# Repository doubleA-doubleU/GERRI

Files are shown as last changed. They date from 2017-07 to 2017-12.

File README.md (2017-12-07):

## GERRI (Guidance Enabled Robotic Raceline Interpreter)
#### _Aaron Weatherly_
#### _Northwestern University_

<p>
<br>

<br>
</p>

## Overview
This project allows an off-the-shelf radio controlled car to be converted
into an autonomous vehicle. This is accomplished by replacing the car's 
control system with an Android phone and a PIC32 microcontroller. External
localization is done through HTC vive position sensors. Check out this 
[video][youtube] for a demonstration.

## Required Components 
1. Android phone (I used a Samsung Galaxy S5)
2. Radio Controlled Car (I used a Tamiya TL01)
3. USB OTG cable - micro to mini
4. 3D printed [phone and PCB mounts][parts]
5. Microchip [PIC32MX250F128B][pic] microcontroller in 28-pin SPDIP package
6. VNH5019 [Motor Driver Carrier][hbridge]
7. HTC Vive [Base Station][base]
8. 2x HTC Vive Position Sensor, [TS3633-CM1][vive]
9. Custom [PCB][pcb] with mounting holes for:
	* 28 Pin DIP socket
	* Mini USB connector
	* Slideswitch
	* MCP1702 voltage regulator (TO92)
	* 3mm red LED with 330 Ohm resistor
	* Reset button with 10 kOhm resistor
	* 3mm green LED with 330 Ohm resistor
	* User button with 10 kOhm resistor
	* 8 MHz crystal resonator
	* 4x 0.1 uF capacitors
	* 2x 10 uF polarized capacitors
	* 5-pin breakout for PICkit3 programmer
	* 2x 8-pin breakouts for remaining I/O pins and power/ground connections

## Software
#### In MPLAB X IDE:
1. Create new 32-bit MPLAB Harmony project, named GERRI, for the PIC32MX250F128B
2. Generate code
3. Copy all code from the provided [app.c][appc], [app.h][apph], 
[main.c][main], [default.mhc][default], [system_config.h][config], 
and [system_interrupt.c][interrupt]	into the auto-generated Harmony 
files of same names
4. Install the project onto the PIC
	
#### In Android Studio:
1. Create new project with an Empty Activity, named GERRI
2. Copy the provided [classes.jar][classes] to <your_local_project_path>/GERRI/app/libs/
3. In the IDE, navigate the left panel to Project/GERRI/app/libs/
4. Right click classes.jar, Add as Library, Add to Module: app
5. In the IDE, navigate the left panel to Android/app/res/
6. Right click res, add driectory, name it "xml"
7. Right click xml, add new XML Resource file, name it "device_filter.xml"
8. Open this new xml file and replace the contents with the code from 
the provided [device_filter.xml][filter] file
9. Copy all code from the provided [activity_main.xml][layout], 
[AndroidManifest.xml][manifest], and [MainActivity.java][java] into 
the auto-generated Android Studio files of same name.

## Under the Hood
This is an extension of a much simpler line-following [robot][pathfinder].

#### The Android app:
GERRI begins by using the phone's camera to identify the track ahead. For
me, the track was designated by blue painter's tape, so the key 
lines from `MainActivity.java` are:
```java
for (int startY = 180; startY <= 300; startY = startY + 20) { // which row in the bitmap to analyze to read
    bmp.getPixels(pixels, 0, bmp.getWidth(), 0, startY, bmp.getWidth(), 1);
    // in the row, see if the pixel is blue
    for (int i = 0; i < bmp.getWidth(); i++) {
        if (blue(pixels[i]) > thresh) {
            pixels[i] = rgb(0, 255, 0); // over write the pixel with pure green
            // COM pixel calculation
            M = M + 1;
            sum = sum + i;
        }
    }
    // update the row
    bmp.setPixels(pixels, 0, bmp.getWidth(), 0, startY, bmp.getWidth(), 1);

    // calculate COM for each row
    if (M == 0) {
        COM = 0;
    } else {
        COM = (sum / M) + 1;
        COMavg += COM;
        count++;
    }
}
```
This loop occurs each time there is a new camera frame. We analyze several
rows of pixels, identify which ones are blue, then calculate the average
position for the portion of the track that can be seen. Then, the following
uses a fixed transform from the camera frame to the world frame to determine
where the track is and add that point to a bitmap representing the track:
```java
// average the COMs
if (count == 0) {
    COMavg = 0;
} else {
    COMavg = COMavg / count;
    // calculate a point on the track based on COMavg, xCar, yCar, theta
    float l = (float) (0.025*COMavg); // distance from left of frame to the COM (in cm)
    float d = (float) (Math.sqrt(Math.pow(18.2,2) - Math.pow(l,2))); // distance from the car to the COM (in cm)
    float theta2 = (float) (Math.atan2(8-l,16.35)); // angle from the car to the COM along a line 16.35 cm from car's position (in radians)
    xTrack = (int) (xCar*100 + d*Math.cos(theta + theta2) + 0.5);
    yTrack = (int) (yCar*100 - 200 + d*Math.sin(theta + theta2) +0.5);
    if (lapTime<0.1) {
        xInit = xTrack;
        yInit = yTrack;
    }
    // add that point to the track bitmap
    if (c2 != null) {
		try {
			bmp2.setPixel(xTrack, yTrack, 0xffffffff);
		} catch (Exception e) {}
    }
}
// draw circle at COM
canvas.drawCircle(COMavg, 240, 5, paint1);
// write the COM as text
canvas.drawText("COM = " + COMavg, 10, 30, paint1);
//send COM to PIC
String sendString = String.valueOf(COMavg) + '\n';
try {
    sPort.write(sendString.getBytes(), 1); // 1 is the timeout
} catch (IOException e) {}
```
This process continues until GERRI has completed its first lap and generated
a map of the entire track. It then switches modes from simple line-following 
to a proportional feedback controller that uses the track bitmap as the desired
path. The first step in this phase is to find the nearest point on the track
from the car's current position:
```java
// find nearest white pixel in bmp2 by looking at the rings of pixels around current location
int x = (int) (xCar*100 + 0.5); // convert to cm
int y = (int) (yCar*100 - 200 + 0.5); // convert to cm, shift to fit the bitmap's range
outerLoop:
for (int ring=0; ring<15;ring++) { // looking within 15cm radius
    int[] pixels = new int[2*ring+1];
    for (int row = -ring; row <= ring; row++) {
        try {
            bmp2.getPixels(pixels,0,bmp2.getWidth(),x-ring,y+row,2*ring+1,1);
        } catch (IllegalArgumentException iae) {} // sometimes the data is bad...
        for (int col = -ring; col <= ring; col++) {
            if (pixels[col+ring] == 0xffffffff) {
                // if the pixel is white, define (xDesired,yDesired) as the current row and column of the search
                xDesired = x+col;
                yDesired = y+row;
                if (xDesired_prev == 0) {
                    xDesired_prev = xDesired;
                    yDesired_prev = yDesired;
                }
                // break the both for loops once the track is found
                break outerLoop;
            }
        }
    }
}
```
Next, we calculate the position and angular error as follows:
```java
// calculate position error
posError = (float) Math.sqrt(Math.pow(xDesired - x,2) + Math.pow(yDesired - y,2));

if (posError != 0 && xDesired - xDesired_prev != 0) {
	// calculate desired angle based on current vs previous track points
    thetaDesired = (float) Math.atan2(yDesired - yDesired_prev, xDesired - xDesired_prev);
    if (Math.abs(thetaDesired-thetaDesired_prev) > 0.5) {
        thetaDesired = thetaDesired_prev;
    }
    // calculate angular error
    angError = thetaDesired - theta;
} else {
    if (thetaDesired_prev == 0){
        thetaDesired = theta;
        angError = 0;
    }
    else {
        thetaDesired = thetaDesired_prev;
        angError = thetaDesired - theta;
    }
}
```
Now we have to determine whether the position error should be positive or
negative by determining whether the track is to the left or right of the
car. There is a hard coded assumption here that the track direction is 
always counterclockwise. This was to simplify the if statements below:
```java
// determine whether track is to the left or right (assuming counterclockwise track direction...)
float theta2 = (float) Math.atan2(yDesired - y, xDesired - x); // angle from car to the track
if (thetaDesired >= Math.PI/2 && thetaDesired < Math.PI) {
    if (theta2 >= Math.PI && theta2 < 3*Math.PI/2) { // the track is to the left of the car
        posError = (-1)*posError;
    }
}
else if (thetaDesired >= Math.PI && thetaDesired < 3*Math.PI/2) {
	if (theta2 >= -Math.PI/2 && theta2 < 0) { // the track is to the left of the car
        posError = (-1)*posError;
    }
}
else if (thetaDesired >= -Math.PI/2 && thetaDesired < 0) {
    if (theta2 >=0 && theta2 < Math.PI/2) { // the track is to the left of the car
        posError = (-1)*posError;
    }
}
else if (thetaDesired >= 0 && thetaDesired < Math.PI/2) {
    if (theta2 >= Math.PI/2 && theta2 < Math.PI) { // the track is to the left of the car
        posError = (-1)*posError;
	}
}
```
Finally, we apply the proportional controller based on the [Stanley method][stanley]
from Stanford's entry into the DARPA Grand Challenge.
```java
// use proportional control to calculate a steering angle value between 0 and 640 based on angError (rad) and posError (cm)
// using the Stanley method: http://robots.stanford.edu/papers/thrun.stanley05.pdf
float cmdRad = angError + (float) Math.atan(thresh2*posError/500); // assuming constant velocity, thresh2 is the proportional gain
float cmdDeg = cmdRad*180/((float) Math.PI);
int cmd;
if (cmdDeg <= -30) {
    cmd = 640;
} else if (cmdDeg >= 30) {
	cmd = 1;
} else {
    cmd = (int) (-320*cmdDeg/30 + 320.5);
}
// send steering command to PIC
String sendString = String.valueOf(cmd) + '\n';
try {
    sPort.write(sendString.getBytes(), 1); // 1 is the timeout
} catch (IOException e) {}
```
In both the mapping and controlled cases, the output of the Android app 
is an integer between 0 and 640 that is proportional to desired steering 
angles between positive and negative 30 degrees that is sent to the PIC.

#### The PIC32 firmware:
The PIC32 communicates with the Android app via USB. It takes the integer value
provided by the app and controlls the motor speed/direction and the servo steering 
angle as shown below (from `app.c`):
```c
if (gotRx) { // rxVal should be an int between 0 and 640 (setting motor speed and steering angle from Center of Mass)
    if (rxVal > 640) {          // stop button pressed, no movement, center the steering, reset lap time
        duty = 0;
        LATAbits.LATA1 = 0;
        LATBbits.LATB2 = 1;
        OC3RS = 1000;
        go = 0;
        lapTime = 0.0;
    } else if (rxVal <= 0) {    // reverse direction and previous steering command to find the line again
        duty = 20;
        LATAbits.LATA1 = 1;     // reverse drive motion
        LATBbits.LATB2 = 0;     // reverse drive motion
        rxVal = rxValPrev;
        OC3RS = 680 + rxValPrev;
        go = 1;
    } else {                    // steer towards the COM
        duty = 20;
        LATAbits.LATA1 = 0;     // forward drive motion
        LATBbits.LATB2 = 1;     // forward drive motion
        OC3RS = 1320 - rxVal;   // ranges from 680 to 1320
        go = 1;
    }
	OC1RS = duty*40;            // convert duty cycle based on period register

    rxPos = 0;
    gotRx = 0; // clear the flag
    rxValPrev = rxVal;
    for (j = 0; j < 64; j++) {
        rx[j] = 0; // clear the array
    }
}
```
The PIC32 also provides the position (x,y,theta) as well as the current lap time to the
Android app via USB (also from `app.c`):
```c
// calculate position
x_pos[0] = (LIGHTHOUSEHEIGHT*sin((x_ang[0])*DEG_TO_RAD))/(sin((60+LIGHTHOUSEANGLE-x_ang[0])*DEG_TO_RAD)*sin((120-LIGHTHOUSEANGLE)*DEG_TO_RAD));
y_pos[0] = (2*LIGHTHOUSEHEIGHT*sin(y_ang[0]*DEG_TO_RAD))/sin((150-y_ang[0])*DEG_TO_RAD);
x_pos[1] = (LIGHTHOUSEHEIGHT*sin((x_ang[1])*DEG_TO_RAD))/(sin((60+LIGHTHOUSEANGLE-x_ang[1])*DEG_TO_RAD)*sin((120-LIGHTHOUSEANGLE)*DEG_TO_RAD));
y_pos[1] = (2*LIGHTHOUSEHEIGHT*sin(y_ang[1]*DEG_TO_RAD))/sin((150-y_ang[1])*DEG_TO_RAD);
x = (x_pos[0] + x_pos[1])/2.0;
y = (y_pos[0] + y_pos[1])/2.0;
        
// calculate angle 
if (x_pos[0] == x_pos[1] && y_pos[0] != y_pos[1]) {
	if (y_pos[0] > y_pos[1]) {
        theta = PHI;
    } else {
        theta = PHI + M_PI;
    }
} else if (y_pos[0] == y_pos[1] && x_pos[0] != x_pos[1]) {
    if (x_pos[1] > x_pos[0]){
        theta = PHI + M_PI_2;
    } else {
        theta = PHI + M_PI_2 + M_PI;
    }
} else if (x_pos[0] == x_pos[1] && y_pos[0] == y_pos[1]) {
    theta = 0.0; // should not happen, as sensors are in two different locations, unless sensors are not receiving data
} else {
    theta = atan2(y_pos[1]-y_pos[0],x_pos[1]-x_pos[0]) + PHI + M_PI_2; // always treating left sensor as origin for angle calc
}
            
// calculate lap time
lapTime = lapTime + ((float) (_CP0_GET_COUNT() - startTime)) / 24000000.0;
               
// send data to phone
len = sprintf(dataOut, "%.3f %.3f %.3f %.3f\r\n", x, y, theta, lapTime);
USB_DEVICE_CDC_Write(USB_DEVICE_CDC_INDEX_0,
    &appData.writeTransferHandle, dataOut, len,
    USB_DEVICE_CDC_TRANSFER_FLAGS_DATA_COMPLETE); 
```
The determination of position is done by `system_interrupt.c` through two ISRs,
one for each of the vive sensors. One of the ISRs is below (and the other is very
similar):
```c
void __ISR(_INPUT_CAPTURE_1_VECTOR, IPL5SOFT) IC1ISR(void) {
    static unsigned int ptsL=0;     // previous time stamp for left sensor
    static int stateL = -1;         // state of left sensor
    unsigned int tsL;               // time stamp for left sensor
    int unusedL = IC1BUF;           // the value of timer2 right now, doesn't matter
    unusedL = IC1BUF;               // read multiple times to ensure the buffer is cleared
    unusedL = IC1BUF;               // ...
    unusedL = IC1BUF;               // ...
    LATBbits.LATB13=PORTAbits.RA4;   // match the sensor signal on a debugging pin
    if (PORTAbits.RA4) {            // ignore rising edges
        IFS0bits.IC1IF = 0;         // clear interrupt flag
        return;                     // exit the ISR
    }    
    tsL = _CP0_GET_COUNT();         // get the current time
    if (ptsL > 0) {                 // won't calculate anything the first time through
        unsigned int l = tsL - ptsL;// calculate elapsed time
        if  (l > CYCLE) {           // indicates a synchronization cycle
            stateL = 0;             // prepare to read y angle (from right to left)
        } else {
            if (stateL >= 0) {
                switch (stateL) {   
                    case 0: {
                        y_ang[0]=l*0.0006;  // read y angle in degrees (0 to 120)
                        break;
                    }
                    case 2: {
                        x_ang[0]=l*0.0006;  // read x angle in degrees (0 to 120)
                        break;
                    }
                }
                stateL++;                       // cycle through states
                if (stateL >=4 ) stateL = -1;   // reset state
            }
        }
    }
    ptsL=tsL;           // set the previous time stamp for the next time through
    IFS0bits.IC1IF = 0; // clear the interrupt flag
}
```
This works because the base station conducts two infrared sweeps, one horizontal and one
vertical. By timing the pulses seen by the sensors, we can determine the angle at which the
base station "sees" the sensor in both directions. With some basic trigonometry, this can
be converted into meters. By doing this with two sensors, the car's heading can also be
determined, as seen above. 

## Future Work
Although this method allows for some autonomous features, it would be ideal to utilize the
track map that is generated to do some more detailed path planning. This could allow for 
the calculation of a racing line that is optimized to decrease the radius of curvature of 
the path and hence the required steering effort of the car.

I also considered including an accelerometer in order to detect loss of traction and 
adjust motor speed accordingly. Due to the limitations on track size based on my workspace,
I decided to use a fixed (and relatively slow) velocity. If the track size were larger,
it would be possible to modulate velocity based on the current error and speed up or slow
down based on the curvature of the track. In that scenario, an accelerometer would be quite 
useful.

[youtube]: https://youtu.be/dq8rHDOIuIY
[parts]: https://github.com/weatherman03/GERRI/tree/master/Parts
[pic]: http://www.microchipdirect.com/product/PIC32MX250F128B
[hbridge]: https://www.pololu.com/product/1451
[base]: https://www.vive.com/us/accessory/base-station/
[vive]: https://www.triadsemi.com/product/ts3633-cm1/
[pcb]: https://github.com/weatherman03/GERRI/tree/master/Eagle
[appc]: https://github.com/weatherman03/GERRI/blob/master/Harmony/app.c
[apph]: https://github.com/weatherman03/GERRI/blob/master/Harmony/app.h
[main]: https://github.com/weatherman03/GERRI/blob/master/Harmony/main.c
[default]: https://github.com/weatherman03/GERRI/blob/master/Harmony/default.mhc
[config]: https://github.com/weatherman03/GERRI/blob/master/Harmony/system_config.h
[interrupt]: https://github.com/weatherman03/GERRI/blob/master/Harmony/system_interrupt.c
[classes]: https://github.com/weatherman03/GERRI/blob/master/Android/classes.jar
[filter]: https://github.com/weatherman03/GERRI/blob/master/Android/device_filter.xml
[layout]: https://github.com/weatherman03/GERRI/blob/master/Android/activity_main.xml
[manifest]: https://github.com/weatherman03/GERRI/blob/master/Android/AndroidManifest.xml
[java]: https://github.com/weatherman03/GERRI/blob/master/Android/MainActivity.java
[pathfinder]: https://github.com/weatherman03/PathFinder
[stanley]: http://robots.stanford.edu/papers/thrun.stanley05.pdf

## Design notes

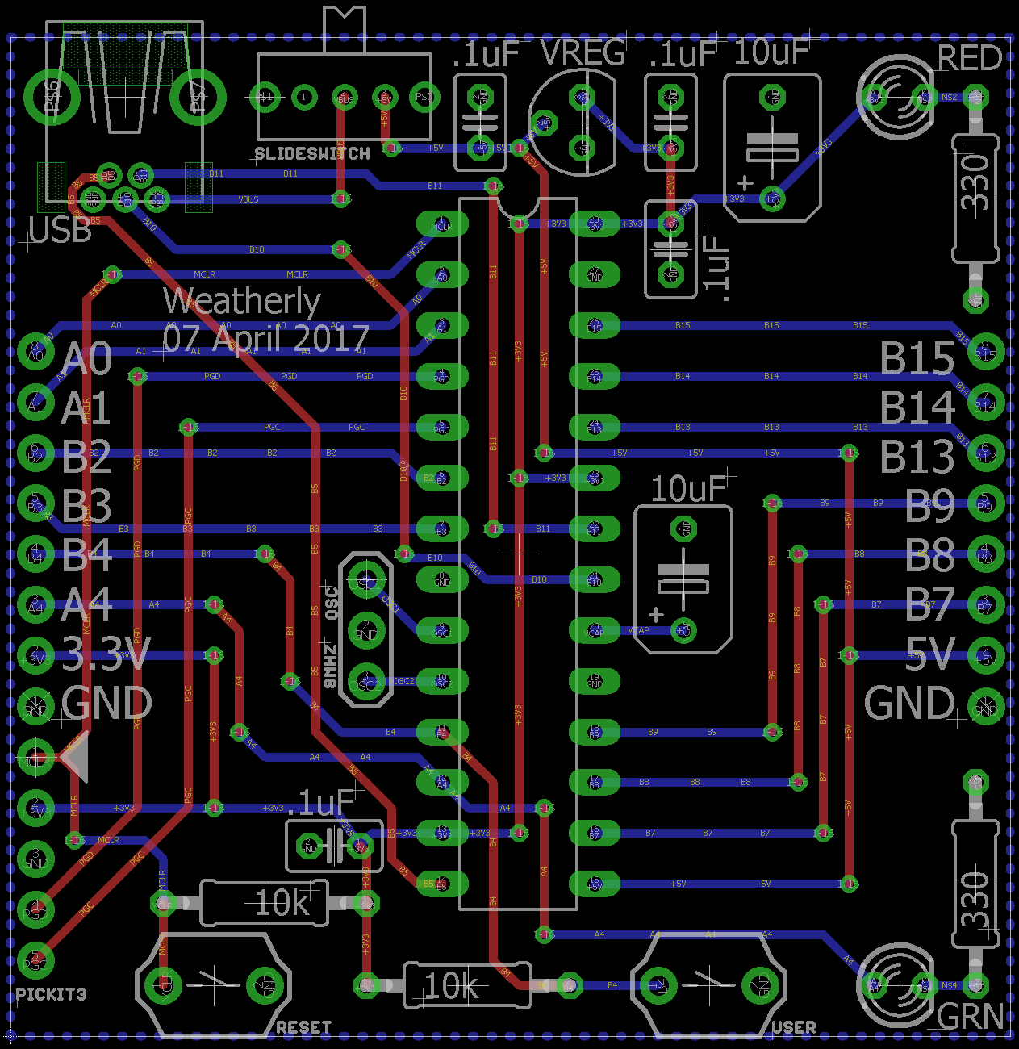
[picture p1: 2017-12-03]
Eagle/PIC32MX250F128B.png

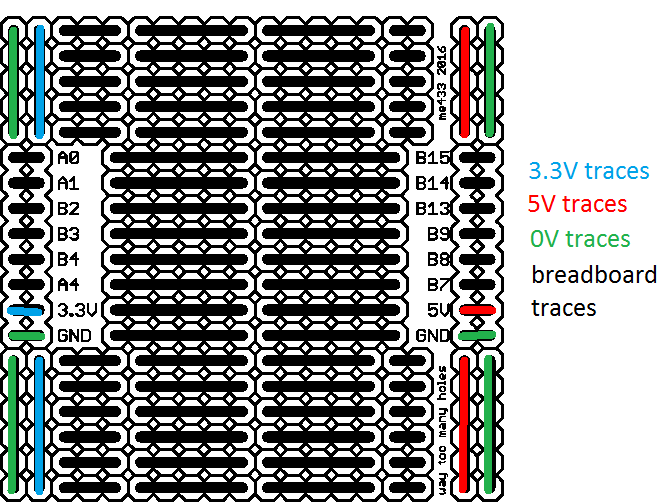
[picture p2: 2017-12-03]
Eagle/pcb_shield.png

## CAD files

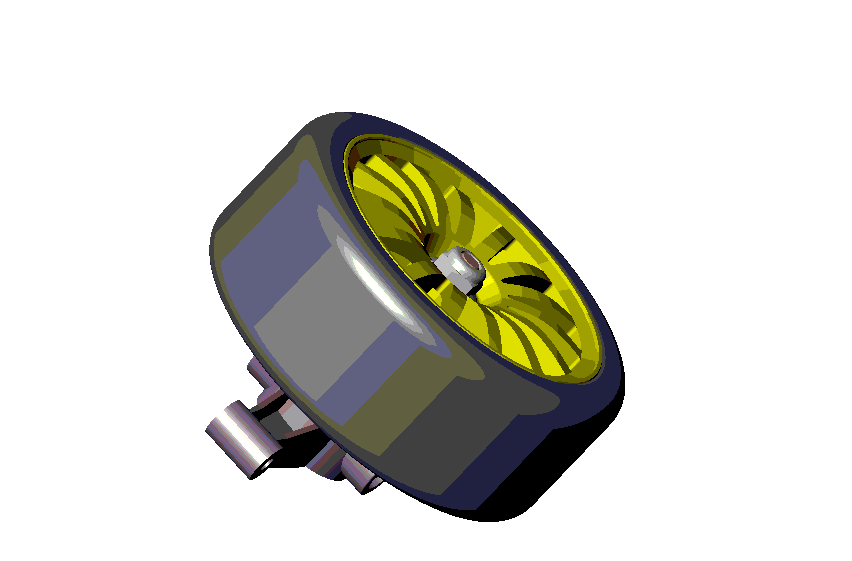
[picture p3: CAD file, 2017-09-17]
Parts/Tamiya TL01/Train-avant.SLDASM
Fusée-av-B9
Coussinet x 2
Axe de roue-MB12
Axe-2-10
Accouplement-B14
Jante
Pneu
Ecrou-MB5

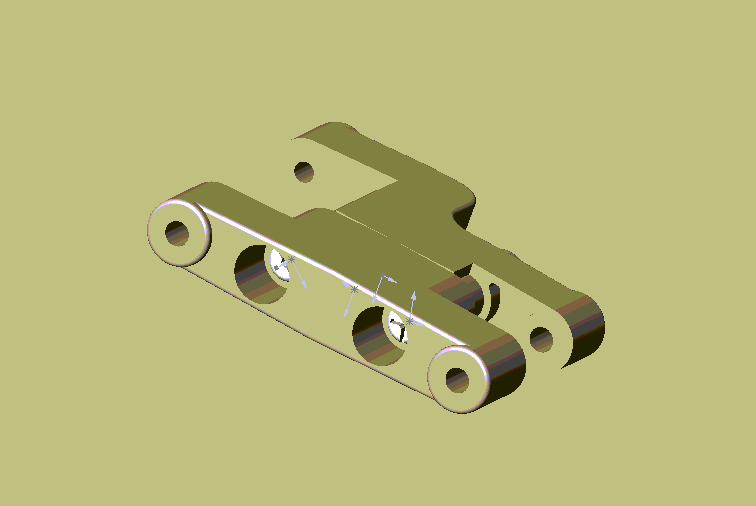
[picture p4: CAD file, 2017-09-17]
Parts/Tamiya TL01/Triangle arrière.SLDASM
Triangle arrière-C15
Triangle arrière-C14
Vis-M3-10 x 2

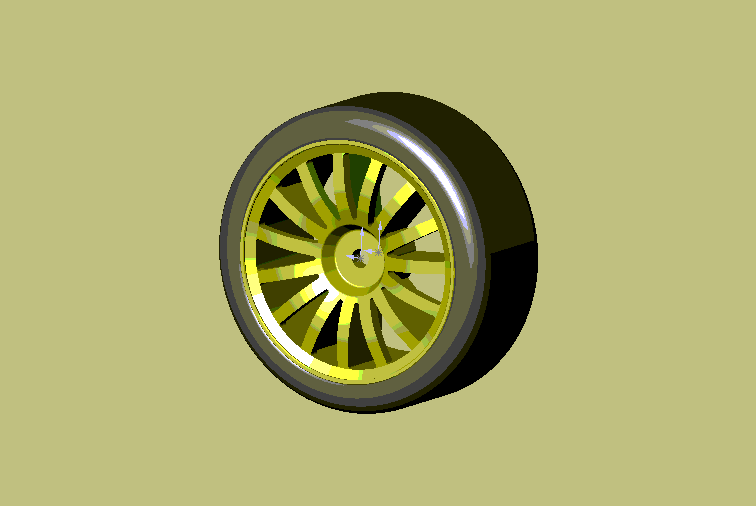
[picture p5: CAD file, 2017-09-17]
Parts/Tamiya TL01/Roue.SLDASM
Jante
Pneu

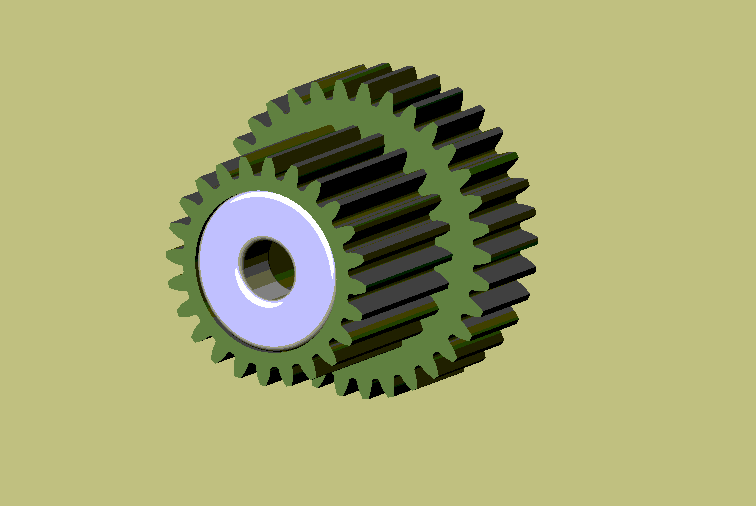
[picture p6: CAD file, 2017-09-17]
Parts/Tamiya TL01/Roue-dentée-2.SLDASM
ENG-D-24-6
ENG-D-34-6
Coussinet x 2

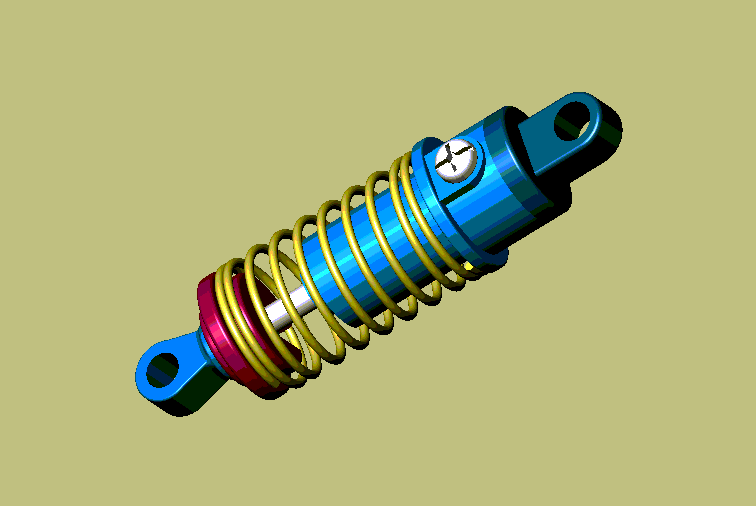
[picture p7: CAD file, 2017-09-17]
Parts/Tamiya TL01/Amortisseur.SLDASM
Corps d'amortisseur-C2
Amortisseur-MB2
Corps d'amortisseur-C1
Amortisseur-C12
Amortisseur-C9
Ressort d'amortisseur-MB14
Vis-M3-10

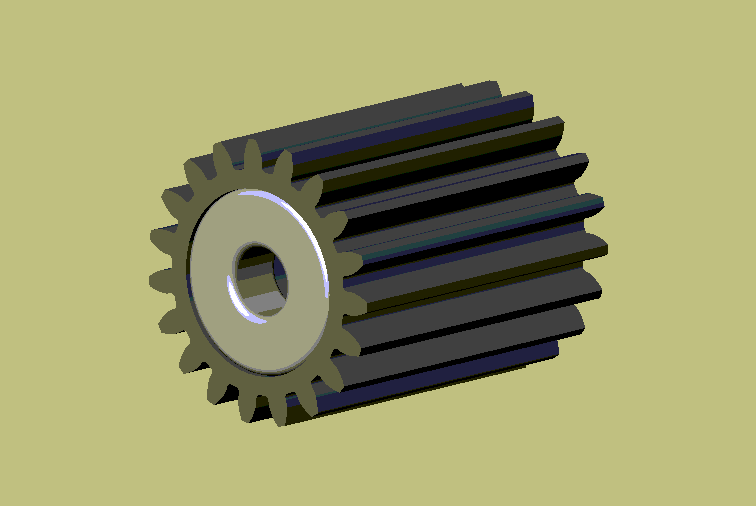
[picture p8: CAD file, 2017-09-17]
Parts/Tamiya TL01/Roue-dentée-6.SLDASM
ENG-D-19-8b
Coussinet x 2

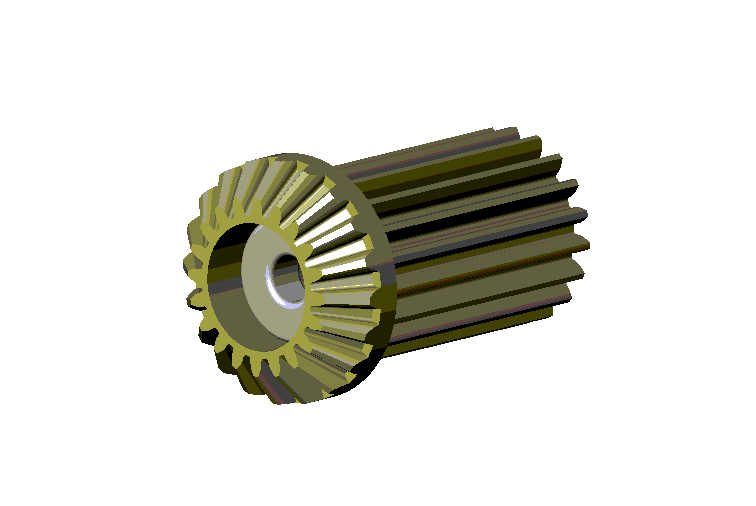
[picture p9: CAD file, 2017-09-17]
Parts/Tamiya TL01/Roue-dentée-5.SLDASM
ENG-D-19-8
ENG-C-20-45
Coussinet x 2

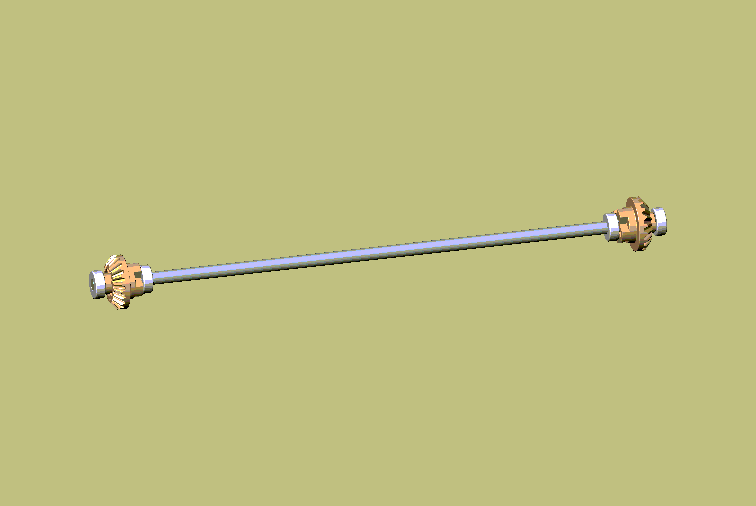
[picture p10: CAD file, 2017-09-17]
Parts/Tamiya TL01/Arbre-transmission.SLDASM
Arbre de transmission
Roue-dentée-4 x 2
Axe-2-10 x 2
Coussinet x 4

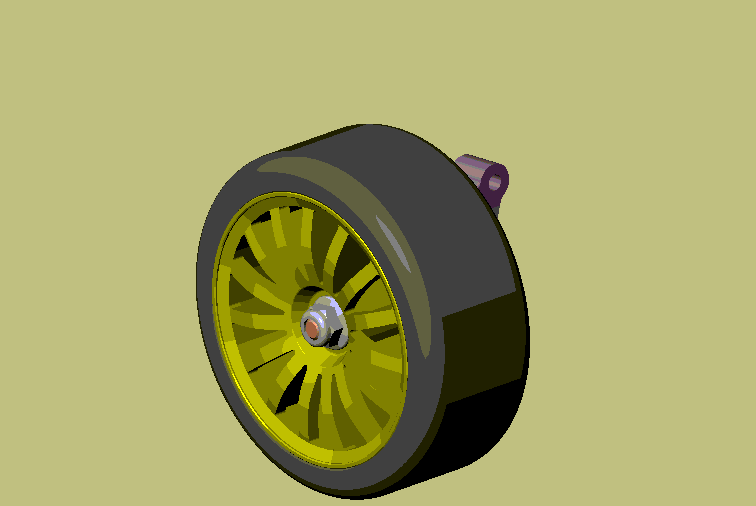
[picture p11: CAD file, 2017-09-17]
Parts/Tamiya TL01/Train-arrière.SLDASM
Fusée-ar-B4
Coussinet x 2
Axe de roue-MB12
Jante
Pneu
Ecrou-MB5
Axe-2-10
Accouplement-B14

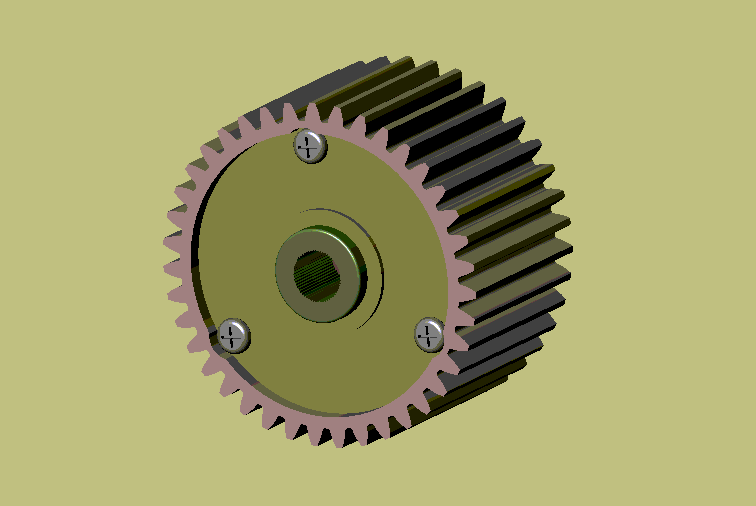
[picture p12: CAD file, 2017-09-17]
Parts/Tamiya TL01/Differentiel.SLDASM
Couronne de différentiel
Différentiel-G3
Différentiel-MA16 x 2
Différentiel-MA18
Différentiel-MA17 x 3
Vis-M2-8 x 3

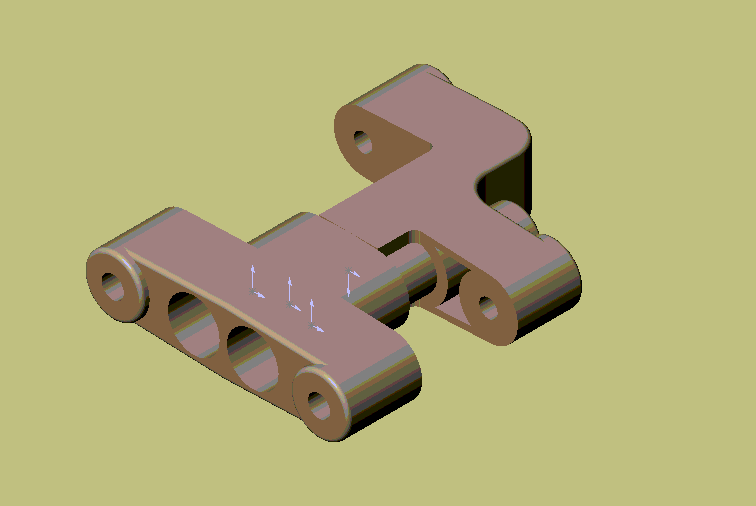
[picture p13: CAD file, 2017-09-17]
Parts/Tamiya TL01/Triangle avant.SLDASM
Triangle avant-C16
Triangle avant-C17
Vis-M3-10 x 2

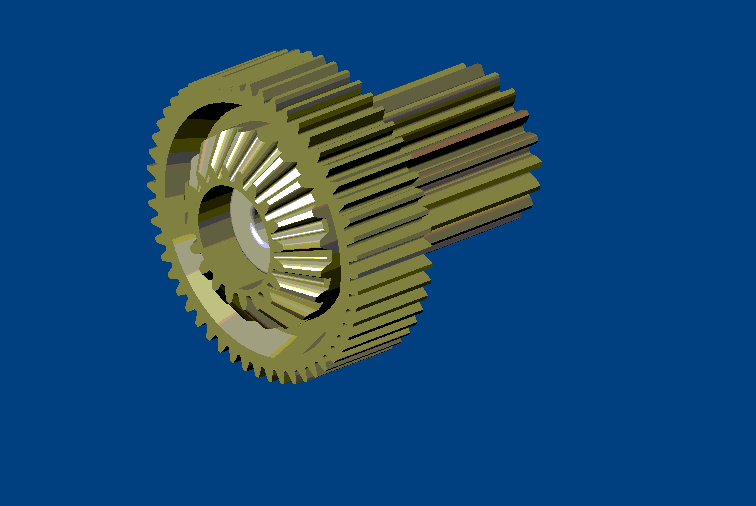
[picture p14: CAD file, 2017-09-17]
Parts/Tamiya TL01/Roue-dentée-3.SLDASM
ENG-D-52-6
ENG-D-19-8
ENG-C-20-45
Coussinet x 2

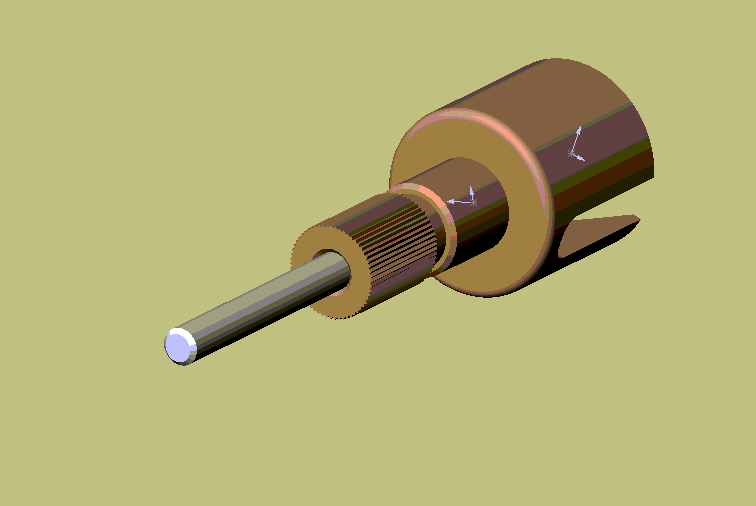
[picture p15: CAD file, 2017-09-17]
Parts/Tamiya TL01/Accouplement-MB11.SLDASM
Accouplement-MB10
Axe-2-27

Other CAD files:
Parts/Tamiya TL01/Transmission-ar-av.SLDASM
Parts/Tamiya TL01/Direction-essai.SLDASM
Parts/Tamiya TL01/Roue-dentée-3b.SLDASM
Parts/Tamiya TL01/Roue-dentée-2b.SLDASM
Parts/Tamiya TL01/Commande de direction.SLDASM
Parts/Tamiya TL01/Accouplement-B14.SLDPRT
Parts/Tamiya TL01/Accouplement-MB10.SLDPRT
Parts/Tamiya TL01/Amortisseur-C12.SLDPRT
Parts/Tamiya TL01/Amortisseur-C9.SLDPRT
Parts/Tamiya TL01/Amortisseur-MB2.SLDPRT
Parts/Tamiya TL01/Antenne-B7.SLDPRT
Parts/Tamiya TL01/Arbre d'entraînement.SLDPRT
Parts/Tamiya TL01/Arbre de transmission.SLDPRT
Parts/Tamiya TL01/Axe de roue-MB12.SLDPRT
Parts/Tamiya TL01/Axe-2-10.SLDPRT
Parts/Tamiya TL01/Axe-2-27.SLDPRT
Parts/Tamiya TL01/Axe-5-25.SLDPRT
Parts/Tamiya TL01/Axe-5-30.SLDPRT
Parts/Tamiya TL01/Axe-5-40.SLDPRT
Parts/Tamiya TL01/Bague de Servomoteur.SLDPRT
Parts/Tamiya TL01/Biellette-C6.SLDPRT
Parts/Tamiya TL01/Capot-B5.SLDPRT
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

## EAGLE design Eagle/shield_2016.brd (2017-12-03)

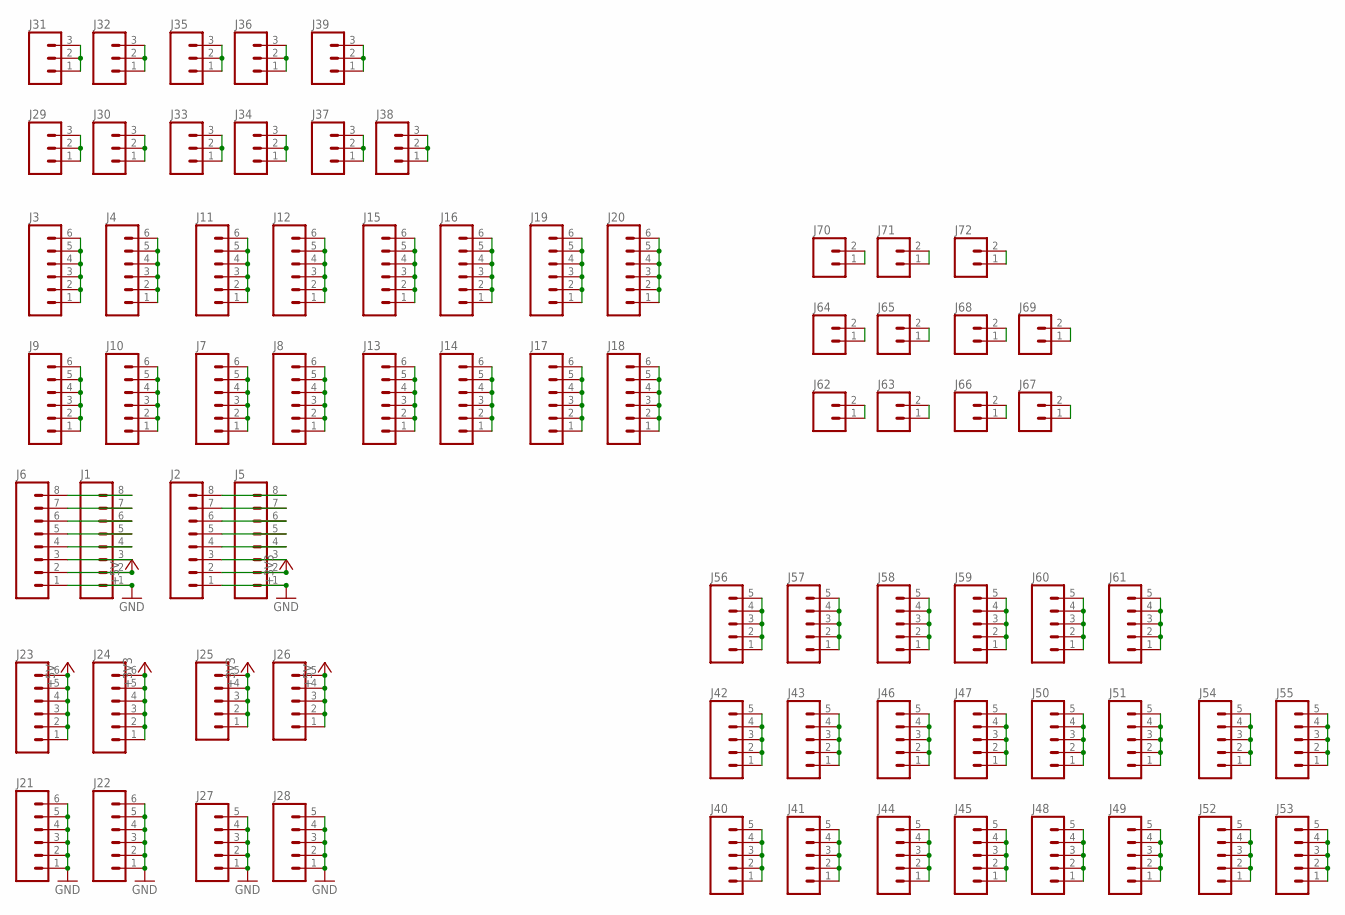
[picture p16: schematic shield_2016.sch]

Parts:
J1, J2, J5, J6: M08; 1X08_ROUND
J3, J4, J7, J8, J9, J10, J11, J12, J13, J14, J15, J16, J17, J18, J19, J20, J21, J22, J23, J24: M06SILK_FEMALE_PTH; 1X06
J25, J26, J27, J28, J40, J41, J42, J43, J44, J45, J46, J47, J48, J49, J50, J51, J52, J53, J54, J55, J56, J57, J58, J59, J60, J61: M05PTH; 1X05
J29, J30, J31, J32, J33, J34, J35, J36, J37, J38, J39: M03PTH; 1X03
J62, J63, J64, J65, J66, J67, J68, J69, J70, J71, J72: M02PTH; 1X02

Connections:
+3V3: J2.2, J5.2, J24.1, J24.2, J24.3, J24.4, J24.5, J24.6, J25.1, J25.2, J25.3, J25.4, J25.5
+5V: J1.2, J6.2, J23.1, J23.2, J23.3, J23.4, J23.5, J23.6, J26.1, J26.2, J26.3, J26.4, J26.5
GND: J1.1, J2.1, J5.1, J6.1, J21.1, J21.2, J21.3, J21.4, J21.5, J21.6, J22.1, J22.2, J22.3, J22.4, J22.5, J22.6, J27.1, J27.2, J27.3, J27.4, J27.5, J28.1, J28.2, J28.3, J28.4, J28.5
unnamed: J3.1, J3.2, J3.3, J3.4, J3.5, J3.6
unnamed: J4.1, J4.2, J4.3, J4.4, J4.5, J4.6
unnamed: J29.1, J29.2, J29.3
unnamed: J30.1, J30.2, J30.3
unnamed: J1.3, J6.3
unnamed: J1.4, J6.4
unnamed: J1.5, J6.5
unnamed: J1.6, J6.6
unnamed: J1.7, J6.7
unnamed: J1.8, J6.8
unnamed: J31.1, J31.2, J31.3
unnamed: J32.1, J32.2, J32.3
unnamed: J2.3, J5.3
unnamed: J2.4, J5.4
unnamed: J2.5, J5.5
unnamed: J2.6, J5.6
unnamed: J2.7, J5.7
unnamed: J2.8, J5.8
unnamed: J7.1, J7.2, J7.3, J7.4, J7.5, J7.6
unnamed: J8.1, J8.2, J8.3, J8.4, J8.5, J8.6
unnamed: J9.1, J9.2, J9.3, J9.4, J9.5, J9.6
unnamed: J10.1, J10.2, J10.3, J10.4, J10.5, J10.6
unnamed: J11.1, J11.2, J11.3, J11.4, J11.5, J11.6
unnamed: J12.1, J12.2, J12.3, J12.4, J12.5, J12.6
unnamed: J13.1, J13.2, J13.3, J13.4, J13.5, J13.6
unnamed: J14.1, J14.2, J14.3, J14.4, J14.5, J14.6
unnamed: J15.1, J15.2, J15.3, J15.4, J15.5, J15.6
unnamed: J16.1, J16.2, J16.3, J16.4, J16.5, J16.6
unnamed: J17.1, J17.2, J17.3, J17.4, J17.5, J17.6
unnamed: J18.1, J18.2, J18.3, J18.4, J18.5, J18.6
unnamed: J19.1, J19.2, J19.3, J19.4, J19.5, J19.6
unnamed: J20.1, J20.2, J20.3, J20.4, J20.5, J20.6
unnamed: J33.1, J33.2, J33.3
unnamed: J34.1, J34.2, J34.3
unnamed: J35.1, J35.2, J35.3
unnamed: J36.1, J36.2, J36.3
unnamed: J37.1, J37.2, J37.3
unnamed: J38.1, J38.2, J38.3
unnamed: J39.1, J39.2, J39.3
unnamed: J40.1, J40.2, J40.3, J40.4, J40.5
unnamed: J41.1, J41.2, J41.3, J41.4, J41.5
unnamed: J42.1, J42.2, J42.3, J42.4, J42.5
unnamed: J43.1, J43.2, J43.3, J43.4, J43.5
unnamed: J44.1, J44.2, J44.3, J44.4, J44.5
unnamed: J45.1, J45.2, J45.3, J45.4, J45.5
unnamed: J46.1, J46.2, J46.3, J46.4, J46.5
unnamed: J47.1, J47.2, J47.3, J47.4, J47.5
unnamed: J48.1, J48.2, J48.3, J48.4, J48.5
unnamed: J49.1, J49.2, J49.3, J49.4, J49.5
unnamed: J50.1, J50.2, J50.3, J50.4, J50.5
unnamed: J51.1, J51.2, J51.3, J51.4, J51.5
unnamed: J52.1, J52.2, J52.3, J52.4, J52.5
unnamed: J53.1, J53.2, J53.3, J53.4, J53.5
unnamed: J54.1, J54.2, J54.3, J54.4, J54.5
unnamed: J55.1, J55.2, J55.3, J55.4, J55.5
unnamed: J56.1, J56.2, J56.3, J56.4, J56.5
unnamed: J57.1, J57.2, J57.3, J57.4, J57.5
unnamed: J58.1, J58.2, J58.3, J58.4, J58.5
unnamed: J59.1, J59.2, J59.3, J59.4, J59.5
unnamed: J60.1, J60.2, J60.3, J60.4, J60.5
unnamed: J61.1, J61.2, J61.3, J61.4, J61.5
unnamed: J62.1, J62.2
unnamed: J63.1, J63.2
unnamed: J64.1, J64.2
unnamed: J65.1, J65.2
unnamed: J66.1, J66.2
unnamed: J67.1, J67.2
unnamed: J68.1, J68.2
unnamed: J69.1, J69.2
unnamed: J70.1, J70.2
unnamed: J71.1, J71.2
unnamed: J72.1, J72.2

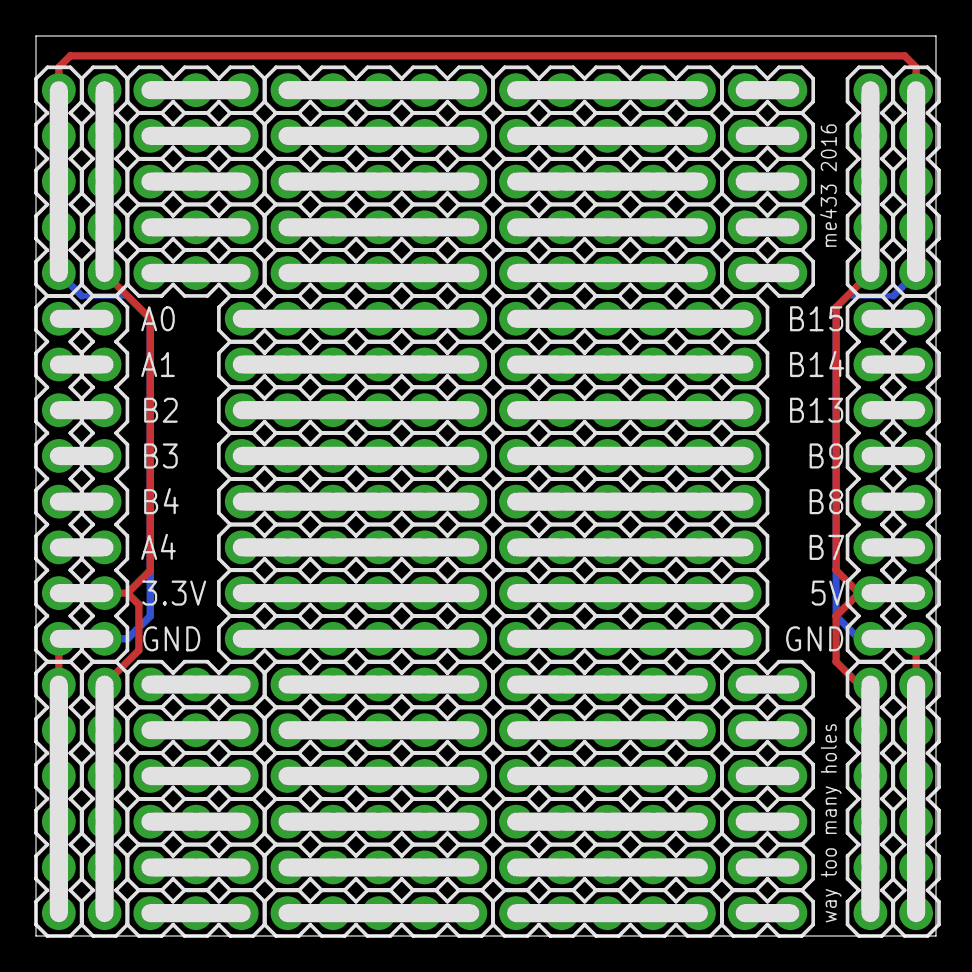
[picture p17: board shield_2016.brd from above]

Board: 2 copper layers, 50.0 x 50.0 mm, 72 parts (0 on the bottom side), 75 nets.

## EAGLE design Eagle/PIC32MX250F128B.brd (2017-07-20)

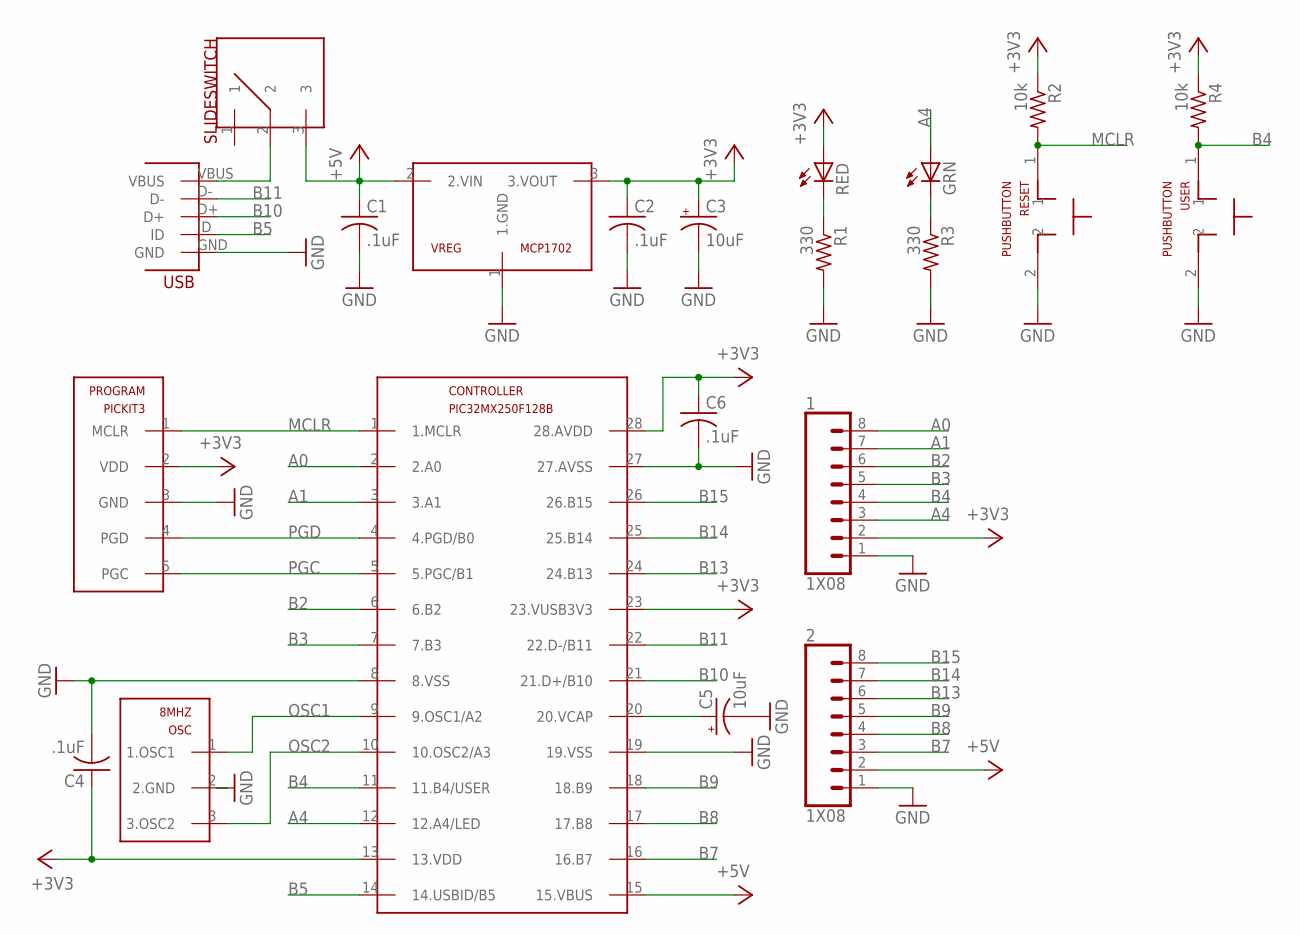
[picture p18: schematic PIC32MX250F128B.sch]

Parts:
1, 2: 1X08; CONN_08
8MHZ: OSC
C1, C2, C4, C6: .1uF; C025-025X050
C3, C5: 10uF; B45181B
CONTROLLER: PIC32MX250F128B; DIL28-3
GRN: LED3MM
PROGRAM: PICKIT3
R1, R3: 330; 0207/10
R2, R4: 10k; 0207/10
RED: LED3MM
RESET: PUSHBUTTON
SLIDESWITCH: SLIDESWITCH
USB: MINIUSB; USB-MB-H
USER: PUSHBUTTON
VREG: MCP1702; TO92

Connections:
+3V3: 1.2, C2.1, C3.+, C4.1, C6.1, CONTROLLER.13 (13.VDD), CONTROLLER.23 (23.VUSB3V3), CONTROLLER.28 (28.AVDD), PROGRAM.2 (VDD), R2.1, R4.1, RED.A, VREG.3 (3.VOUT)
+5V: 2.2, C1.1, CONTROLLER.15 (15.VBUS), SLIDESWITCH.3, VREG.2 (2.VIN)
A0: 1.8, CONTROLLER.2 (2.A0)
A1: 1.7, CONTROLLER.3 (3.A1)
A4: 1.3, CONTROLLER.12 (12.A4/LED), GRN.A
B2: 1.6, CONTROLLER.6 (6.B2)
B3: 1.5, CONTROLLER.7 (7.B3)
B4: 1.4, CONTROLLER.11 (11.B4/USER), R4.2, USER.1
B5: CONTROLLER.14 (14.USBID/B5), USB.ID
B7: 2.3, CONTROLLER.16 (16.B7)
B8: 2.4, CONTROLLER.17 (17.B8)
B9: 2.5, CONTROLLER.18 (18.B9)
B10: CONTROLLER.21 (21.D+/B10), USB.D+
B11: CONTROLLER.22 (22.D-/B11), USB.D-
B13: 2.6, CONTROLLER.24 (24.B13)
B14: 2.7, CONTROLLER.25 (25.B14)
B15: 2.8, CONTROLLER.26 (26.B15)
GND: 1.1, 2.1, 8MHZ.2 (2.GND), C1.2, C2.2, C3.-, C4.2, C5.-, C6.2, CONTROLLER.8 (8.VSS), CONTROLLER.19 (19.VSS), CONTROLLER.27 (27.AVSS), PROGRAM.3 (GND), R1.2, R3.2, RESET.2, USB.GND, USER.2, VREG.1 (1.GND)
MCLR: CONTROLLER.1 (1.MCLR), PROGRAM.1 (MCLR), R2.2, RESET.1
unnamed: R1.1, RED.K (C)
unnamed: GRN.K (C), R3.1
OSC1: 8MHZ.1 (1.OSC1), CONTROLLER.9 (9.OSC1/A2)
OSC2: 8MHZ.3 (3.OSC2), CONTROLLER.10 (10.OSC2/A3)
PGC: CONTROLLER.5 (5.PGC/B1), PROGRAM.5 (PGC)
PGD: CONTROLLER.4 (4.PGD/B0), PROGRAM.4 (PGD)
VBUS: SLIDESWITCH.2, USB.VBUS
VCAP: C5.+, CONTROLLER.20 (20.VCAP)

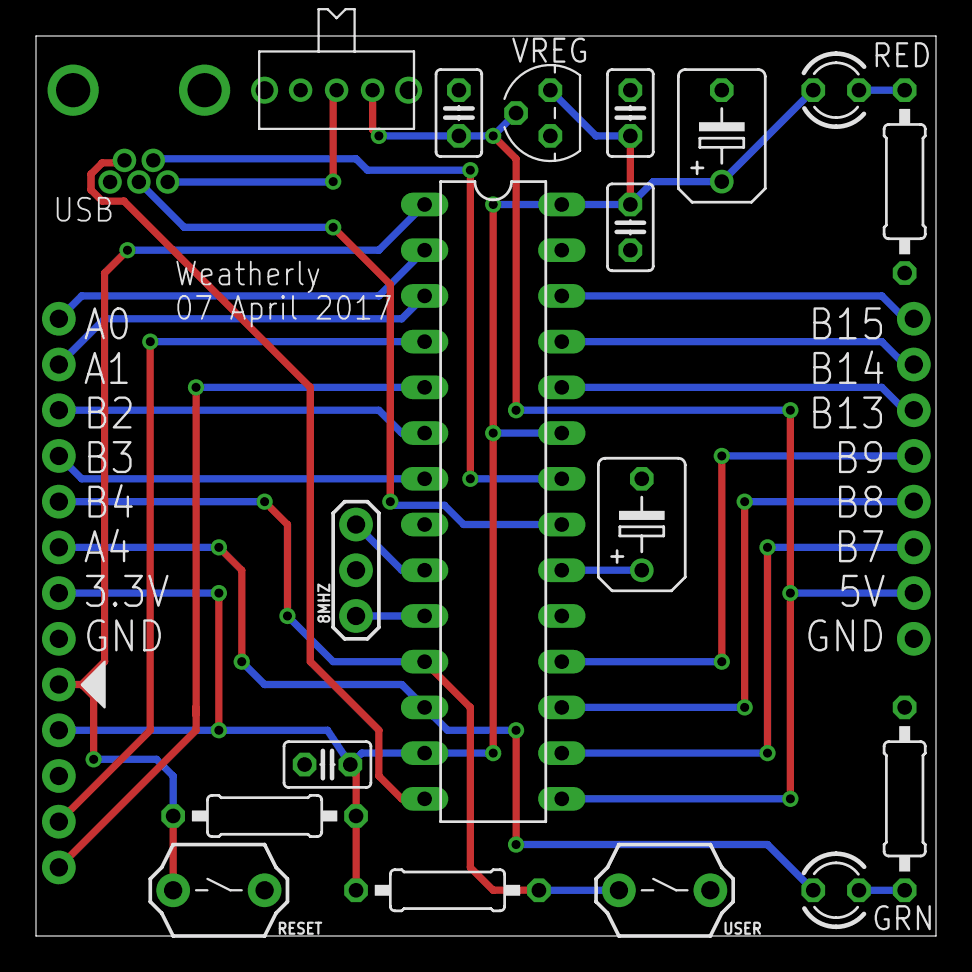
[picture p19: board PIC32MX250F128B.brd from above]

Board: 2 copper layers, 50.0 x 50.0 mm, 22 parts (0 on the bottom side), 27 nets.

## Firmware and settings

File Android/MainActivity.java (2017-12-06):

package com.example.aaron.gerri;

// libraries
import android.Manifest;
import android.app.Activity;
import android.app.PendingIntent;
import android.content.Context;
import android.content.Intent;
import android.content.pm.PackageManager;
import android.graphics.Bitmap;
import android.graphics.Canvas;
import android.graphics.Paint;
import android.graphics.SurfaceTexture;
import android.hardware.Camera;
import android.hardware.usb.UsbDeviceConnection;
import android.hardware.usb.UsbManager;
import android.os.Bundle;
import android.support.v4.content.ContextCompat;
import android.view.SurfaceHolder;
import android.view.SurfaceView;
import android.view.TextureView;
import android.view.View;
import android.view.WindowManager;
import android.widget.Button;
import android.widget.TextView;
import android.widget.SeekBar;
import android.widget.SeekBar.OnSeekBarChangeListener;

import com.hoho.android.usbserial.driver.CdcAcmSerialDriver;
import com.hoho.android.usbserial.driver.ProbeTable;
import com.hoho.android.usbserial.driver.UsbSerialDriver;
import com.hoho.android.usbserial.driver.UsbSerialPort;
import com.hoho.android.usbserial.driver.UsbSerialProber;
import com.hoho.android.usbserial.util.SerialInputOutputManager;

import java.io.IOException;
import java.io.UnsupportedEncodingException;
import java.util.List;
import java.util.Scanner;
import java.util.concurrent.ExecutorService;
import java.util.concurrent.Executors;

import static android.graphics.Color.blue;
import static android.graphics.Color.rgb;

public class MainActivity extends Activity implements TextureView.SurfaceTextureListener {
    private Camera mCamera;
    private TextureView mTextureView;
    private SurfaceView mSurfaceView;
    private SurfaceView mSurfaceView2;
    private SurfaceHolder mSurfaceHolder;
    private SurfaceHolder mSurfaceHolder2;
    private Bitmap bmp = Bitmap.createBitmap(640, 480, Bitmap.Config.ARGB_8888);
    private Canvas canvas = new Canvas(bmp);
    private Bitmap bmp2 = Bitmap.createBitmap(500, 400, Bitmap.Config.ARGB_8888);
    private Paint paint1 = new Paint();
    private TextView myTextView;
    private TextView myTextView2;
    private TextView myTextView3;
    private SeekBar threshold;
    private SeekBar threshold2;
    private Button button;
    int thresh = 120;
    int thresh2 = 10;
    int go = -1;
    int xTrack = 0, yTrack = 0, xInit = 0, yInit = 0, xDesired_prev = 0, yDesired_prev = 0, xDesired, yDesired;
    float xCar = 0, yCar = 0, theta = 0, lapTime = 0, thetaDesired_prev = 0, thetaDesired, angError, posError;

    private UsbManager manager;
    private UsbSerialPort sPort;
    private final ExecutorService mExecutor = Executors.newSingleThreadExecutor();
    private SerialInputOutputManager mSerialIoManager;

    protected void onCreate(Bundle savedInstanceState) {
        super.onCreate(savedInstanceState);
        setContentView(R.layout.activity_main);
        getWindow().addFlags(WindowManager.LayoutParams.FLAG_KEEP_SCREEN_ON); // keeps the screen from turning off

        threshold = (SeekBar) findViewById(R.id.seek1);
        threshold2 = (SeekBar) findViewById(R.id.seek2);
        myTextView = (TextView) findViewById(R.id.textView01);
        myTextView2 = (TextView) findViewById(R.id.textView02);
        myTextView3 = (TextView) findViewById(R.id.textView03);
        button = (Button) findViewById(R.id.button1);

        button.setOnClickListener(new View.OnClickListener() {
            @Override
            public void onClick(View v) { // change state variable
                go = go + 2;
                if (go > 2) {
                    go = -1;
                    // send 641 to the PIC to stop motors (outside of expected range for COM)
                    String sendString = String.valueOf(641) + '\n';
                    for (int j = 0; j < 5; j++) { // send multiple times to make sure the robot "hears" it
                        try {
                            sPort.write(sendString.getBytes(), 1); // 1 is the timeout
                        } catch (IOException e) {
                        }
                    }
                }
            }
        });

        // see if the app has permission to use the camera
        //ActivityCompat.requestPermissions(MainActivity.this, new String[]{Manifest.permission.CAMERA}, 1);
        if (ContextCompat.checkSelfPermission(this, Manifest.permission.CAMERA) == PackageManager.PERMISSION_GRANTED) {
            mSurfaceView = (SurfaceView) findViewById(R.id.surfaceview);
            mSurfaceHolder = mSurfaceView.getHolder();

            mSurfaceView2 = (SurfaceView) findViewById(R.id.surfaceview2);
            mSurfaceHolder2 = mSurfaceView2.getHolder();

            mTextureView = (TextureView) findViewById(R.id.textureview);
            mTextureView.setSurfaceTextureListener(this);

            // set the paintbrush for writing text on the image
            paint1.setColor(0xffff0000); // red
            paint1.setTextSize(24);
        }

        setMyControlListener();
        manager = (UsbManager) getSystemService(Context.USB_SERVICE);
    }

    public void onSurfaceTextureAvailable(SurfaceTexture surface, int width, int height) {
        mCamera = Camera.open(); // might crash here if native camera app is running
        Camera.Parameters parameters = mCamera.getParameters();
        parameters.setPreviewSize(640, 480);
        parameters.setFocusMode(Camera.Parameters.FOCUS_MODE_INFINITY); // no autofocusing
        parameters.setAutoExposureLock(false); // auto exposure is on
        mCamera.setParameters(parameters);
        mCamera.setDisplayOrientation(90); // rotate to portrait mode

        try {
            mCamera.setPreviewTexture(surface);
            mCamera.startPreview();
        } catch (IOException ioe) {
            // Something bad happened
        }
    }

    public void onSurfaceTextureSizeChanged(SurfaceTexture surface, int width, int height) {
        // Ignored, Camera does all the work for us
    }

    public boolean onSurfaceTextureDestroyed(SurfaceTexture surface) {
        mCamera.stopPreview();
        mCamera.release();
        return true;
    }

    // SeekBars
    private void setMyControlListener() {
        threshold.setOnSeekBarChangeListener(new OnSeekBarChangeListener() {

            @Override
            public void onProgressChanged(SeekBar seekBar, int progress, boolean fromUser) {
                thresh = progress;
                myTextView.setText("Blue Greater Than: "+thresh);
            }

            @Override
            public void onStartTrackingTouch(SeekBar seekBar) {
            }

            @Override
            public void onStopTrackingTouch(SeekBar seekBar) {
            }
        });

        threshold2.setOnSeekBarChangeListener(new OnSeekBarChangeListener() {

            @Override
            public void onProgressChanged(SeekBar seekBar, int progress, boolean fromUser) {
                thresh2 = progress;
                myTextView3.setText("Proportional Gain: "+thresh2);
            }

            @Override
            public void onStartTrackingTouch(SeekBar seekBar) {
            }

            @Override
            public void onStopTrackingTouch(SeekBar seekBar) {
            }
        });
    }

    // USB functionality
    private final SerialInputOutputManager.Listener mListener =
            new SerialInputOutputManager.Listener() {
                @Override
                public void onRunError(Exception e) {

                }

                @Override
                public void onNewData(final byte[] data) {
                    MainActivity.this.runOnUiThread(new Runnable() {
                        @Override
                        public void run() {
                            MainActivity.this.updateReceivedData(data);
                        }
                    });
                }
            };

    @Override
    protected void onPause(){
        super.onPause();
        stopIoManager();
        if(sPort != null){
            try{
                sPort.close();
            } catch (IOException e){ }
            sPort = null;
        }
        finish();
    }

    @Override
    protected void onResume() {
        super.onResume();

        ProbeTable customTable = new ProbeTable();
        customTable.addProduct(0x04D8,0x000A, CdcAcmSerialDriver.class);
        UsbSerialProber prober = new UsbSerialProber(customTable);

        final List<UsbSerialDriver> availableDrivers = prober.findAllDrivers(manager);

        if(availableDrivers.isEmpty()) {
            //check
            return;
        }

        UsbSerialDriver driver = availableDrivers.get(0);
        sPort = driver.getPorts().get(0);

        if (sPort == null){
            //check
        }else{
            final UsbManager usbManager = (UsbManager) getSystemService(Context.USB_SERVICE);
            UsbDeviceConnection connection = usbManager.openDevice(driver.getDevice());
            if (connection == null){
                //check
                PendingIntent pi = PendingIntent.getBroadcast(this, 0, new Intent("com.android.example.USB_PERMISSION"), 0);
                usbManager.requestPermission(driver.getDevice(), pi);
                return;
            }

            try {
                sPort.open(connection);
                sPort.setParameters(9600, 8, UsbSerialPort.STOPBITS_1, UsbSerialPort.PARITY_NONE);

            }catch (IOException e) {
                //check
                try{
                    sPort.close();
                } catch (IOException e1) { }
                sPort = null;
                return;
            }
        }
        onDeviceStateChange();
    }

    private void stopIoManager(){
        if(mSerialIoManager != null) {
            mSerialIoManager.stop();
            mSerialIoManager = null;
        }
    }

    private void startIoManager() {
        if(sPort != null){
            mSerialIoManager = new SerialInputOutputManager(sPort, mListener);
            mExecutor.submit(mSerialIoManager);
        }
    }

    private void onDeviceStateChange(){
        stopIoManager();
        startIoManager();
    }

    private void updateReceivedData(byte[] data) {

        // store received data in the xCar,yCar,theta,lapTime variables
        if (go > 0) {
            String rxString = null;
            try {
                rxString = new String(data, "UTF-8"); // put the data you got into a string
                Scanner scan = new Scanner(rxString);
                float buffer[] = new float[4];
                int i = 0;
                while (scan.hasNextFloat()) {
                    buffer[i] = scan.nextFloat();
                    i++;
                }
                xCar = buffer[0]; // in meters
                yCar = buffer[1]; // in meters
                theta = buffer[2]; // in radians
                lapTime = buffer[3]; // in seconds
            } catch (UnsupportedEncodingException e) {
                e.printStackTrace();
            }
        }
    }

    // the important function
    public void onSurfaceTextureUpdated(SurfaceTexture surface) {
        int M, sum, COM, COMavg, count;
        if (go == 1) {
            M = 0;
            sum = 0;
            COMavg = 0;
            count = 0;
            // every time there is a new Camera preview frame
            mTextureView.getBitmap(bmp);

            final Canvas c = mSurfaceHolder.lockCanvas();
            final Canvas c2 = mSurfaceHolder2.lockCanvas();
            if (c != null) {
                int[] pixels = new int[bmp.getWidth()]; // pixels[] is the RGBA data
                for (int startY = 180; startY <= 300; startY = startY + 20) { // which row in the bitmap to analyze to read
                    bmp.getPixels(pixels, 0, bmp.getWidth(), 0, startY, bmp.getWidth(), 1);
                    // in the row, see if the pixel is blue
                    for (int i = 0; i < bmp.getWidth(); i++) {
                        if (blue(pixels[i]) > thresh) {
                            pixels[i] = rgb(0, 255, 0); // over write the pixel with pure green
                            // COM pixel calculation
                            M = M + 1;
                            sum = sum + i;
                        }
                    }
                    // update the row
                    bmp.setPixels(pixels, 0, bmp.getWidth(), 0, startY, bmp.getWidth(), 1);

                    // calculate COM for each row
                    if (M == 0) {
                        COM = 0;
                    } else {
                        COM = (sum / M) + 1;
                        COMavg += COM;
                        count++;
                    }
                }
                // average the COMs
                if (count == 0) {
                    COMavg = 0;
                } else {
                    COMavg = COMavg / count;
                    // calculate a point on the track based on COMavg, xCar, yCar, theta
                    float l = (float) (0.025*COMavg); // distance from left of frame to the COM (in cm)
                    float d = (float) (Math.sqrt(Math.pow(18.2,2) - Math.pow(l,2))); // distance from the car to the COM (in cm)
                    float theta2 = (float) (Math.atan2(8-l,16.35)); // angle from the car to the COM along a line 16.35 cm from car's position (in radians)
                    xTrack = (int) (xCar*100 + d*Math.cos(theta + theta2) + 0.5);
                    yTrack = (int) (yCar*100 - 200 + d*Math.sin(theta + theta2) +0.5);
                    if (lapTime<0.1) {
                        xInit = xTrack;
                        yInit = yTrack;
                    }
                    // add that point to the track bitmap
                    if (c2 != null) {
                        try {
                            bmp2.setPixel(xTrack, yTrack, 0xffffffff);
                        } catch (Exception e) {}
                    }
                }
                // draw circle at COM
                canvas.drawCircle(COMavg, 240, 5, paint1);
                // write the COM as text
                canvas.drawText("COM = " + COMavg, 10, 30, paint1);
                //send COM to PIC
                String sendString = String.valueOf(COMavg) + '\n';
                try {
                    sPort.write(sendString.getBytes(), 1); // 1 is the timeout
                } catch (IOException e) {}
            }
            c.drawBitmap(bmp, 0, 0, null);
            mSurfaceHolder.unlockCanvasAndPost(c);
            c2.drawBitmap(bmp2, 0, 0, null);
            mSurfaceHolder2.unlockCanvasAndPost(c2);

            // lap complete condition
            double dist_from_start = Math.sqrt(Math.pow(xCar*100 - xInit,2) + Math.pow(yCar*100 - 200 - yInit,2));
            if (lapTime>10 && dist_from_start <= 5) {
                go = 2;
            }
            myTextView2.setText(String.format("pos = (%d, %d) t = %f", (int) (xCar*100 + 0.5), (int) (yCar*100 - 200 + 0.5), lapTime));
        }
        // once the first lap is complete, follow line based on feedback control using bmp2 as desired path
        if (go == 2) {
            // find nearest white pixel in bmp2 by looking at the rings of pixels around current location
            int x = (int) (xCar*100 + 0.5);
            int y = (int) (yCar*100 - 200 + 0.5);
            outerLoop:
            for (int ring=0; ring<15;ring++) { // looking within 15cm radius
                int[] pixels = new int[2*ring+1];
                for (int row = -ring; row <= ring; row++) {
                    try {
                        bmp2.getPixels(pixels,0,bmp2.getWidth(),x-ring,y+row,2*ring+1,1);
                    } catch (IllegalArgumentException iae) {} // sometimes the data is bad...
                    for (int col = -ring; col <= ring; col++) {
                        if (pixels[col+ring] == 0xffffffff) {
                            // if the pixel is white, define (xDesired,yDesired) as the current row and column of the search
                            xDesired = x+col;
                            yDesired = y+row;
                            if (xDesired_prev == 0) {
                                xDesired_prev = xDesired;
                                yDesired_prev = yDesired;
                            }
                            // break the both for loops once the track is found
                            break outerLoop;
                        }
                    }
                }
            }
            // calculate position error
            posError = (float) Math.sqrt(Math.pow(xDesired - x,2) + Math.pow(yDesired - y,2));

            if (posError != 0 && xDesired - xDesired_prev != 0) {
                // calculate desired angle based on current vs previous track points
                thetaDesired = (float) Math.atan2(yDesired - yDesired_prev, xDesired - xDesired_prev);
                if (Math.abs(thetaDesired-thetaDesired_prev) > 0.5) {
                    thetaDesired = thetaDesired_prev;
                }
                // calculate angular error
                angError = thetaDesired - theta;
            } else {
                if (thetaDesired_prev == 0){
                    thetaDesired = theta;
                    angError = 0;
                }
                else {
                    thetaDesired = thetaDesired_prev;
                    angError = thetaDesired - theta;
                }
            }
            xDesired_prev = xDesired;
            yDesired_prev = yDesired;
            thetaDesired_prev = thetaDesired;

            // determine whether track is to the left or right (assuming counterclockwise track direction...)
            float theta2 = (float) Math.atan2(yDesired - y, xDesired - x); // angle from car to the track
            if (thetaDesired >= Math.PI/2 && thetaDesired < Math.PI) {
                if (theta2 >= Math.PI && theta2 < 3*Math.PI/2) { // the track is to the left of the car
                    posError = (-1)*posError;
                }
            }
            else if (thetaDesired >= Math.PI && thetaDesired < 3*Math.PI/2) {
                if (theta2 >= -Math.PI/2 && theta2 < 0) { // the track is to the left of the car
                    posError = (-1)*posError;
                }
            }
            else if (thetaDesired >= -Math.PI/2 && thetaDesired < 0) {
                if (theta2 >=0 && theta2 < Math.PI/2) { // the track is to the left of the car
                    posError = (-1)*posError;
                }
            }
            else if (thetaDesired >= 0 && thetaDesired < Math.PI/2) {
                if (theta2 >= Math.PI/2 && theta2 < Math.PI) { // the track is to the left of the car
                    posError = (-1)*posError;
                }
            }

            // use proportional control to calculate a steering angle value between 0 and 640 based on angError (rad) and posError (cm)
            // using the Stanley method: http://robots.stanford.edu/papers/thrun.stanley05.pdf
            float cmdRad = angError + (float) Math.atan(thresh2*posError/500); // assuming constant velocity, thresh2 is the proportional gain
            float cmdDeg = cmdRad*180/((float) Math.PI);
            int cmd;
            if (cmdDeg <= -30) {
                cmd = 640;
            } else if (cmdDeg >= 30) {
                cmd = 1;
            } else {
                cmd = (int) (-320*cmdDeg/30 + 320.5);
            }
            // send steering command to PIC
            String sendString = String.valueOf(cmd) + '\n';
            try {
                sPort.write(sendString.getBytes(), 1); // 1 is the timeout
            } catch (IOException e) {}
            myTextView2.setText(String.format("posError= %f angError= %f", posError, angError));
        }
    }
}

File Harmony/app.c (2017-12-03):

/*******************************************************************************
  MPLAB Harmony Application Source File
  
  Company:
    Microchip Technology Inc.
  
  File Name:
    app.c

  Summary:
    This file contains the source code for the MPLAB Harmony application.

  Description:
    This file contains the source code for the MPLAB Harmony application.  It 
    implements the logic of the application's state machine and it may call 
    API routines of other MPLAB Harmony modules in the system, such as drivers,
    system services, and middleware.  However, it does not call any of the
    system interfaces (such as the "Initialize" and "Tasks" functions) of any of
    the modules in the system or make any assumptions about when those functions
    are called.  That is the responsibility of the configuration-specific system
    files.
 *******************************************************************************/

// DOM-IGNORE-BEGIN
/*******************************************************************************
Copyright (c) 2013-2014 released Microchip Technology Inc.  All rights reserved.

Microchip licenses to you the right to use, modify, copy and distribute
Software only when embedded on a Microchip microcontroller or digital signal
controller that is integrated into your product or third party product
(pursuant to the sublicense terms in the accompanying license agreement).

You should refer to the license agreement accompanying this Software for
additional information regarding your rights and obligations.

SOFTWARE AND DOCUMENTATION ARE PROVIDED "AS IS" WITHOUT WARRANTY OF ANY KIND,
EITHER EXPRESS OR IMPLIED, INCLUDING WITHOUT LIMITATION, ANY WARRANTY OF
MERCHANTABILITY, TITLE, NON-INFRINGEMENT AND FITNESS FOR A PARTICULAR PURPOSE.
IN NO EVENT SHALL MICROCHIP OR ITS LICENSORS BE LIABLE OR OBLIGATED UNDER
CONTRACT, NEGLIGENCE, STRICT LIABILITY, CONTRIBUTION, BREACH OF WARRANTY, OR
OTHER LEGAL EQUITABLE THEORY ANY DIRECT OR INDIRECT DAMAGES OR EXPENSES
INCLUDING BUT NOT LIMITED TO ANY INCIDENTAL, SPECIAL, INDIRECT, PUNITIVE OR
CONSEQUENTIAL DAMAGES, LOST PROFITS OR LOST DATA, COST OF PROCUREMENT OF
SUBSTITUTE GOODS, TECHNOLOGY, SERVICES, OR ANY CLAIMS BY THIRD PARTIES
(INCLUDING BUT NOT LIMITED TO ANY DEFENSE THEREOF), OR OTHER SIMILAR COSTS.
 *******************************************************************************/
// DOM-IGNORE-END


// *****************************************************************************
// *****************************************************************************
// Section: Included Files 
// *****************************************************************************
// *****************************************************************************

#include "app.h"
#include <stdio.h>
#include <xc.h>
#include <math.h>

// *****************************************************************************
// *****************************************************************************
// Section: Global Data Definitions
// *****************************************************************************
// *****************************************************************************


// *****************************************************************************
/* Application Data

  Summary:
    Holds application data

  Description:
    This structure holds the application's data.

  Remarks:
    This structure should be initialized by the APP_Initialize function.
    
    Application strings and buffers are be defined outside this structure.
 */

APP_DATA appData;

// *****************************************************************************
// *****************************************************************************
// Section: Application Callback Functions
// *****************************************************************************
// *****************************************************************************

/* TODO:  Add any necessary callback functions.
 */

/*******************************************************
 * USB CDC Device Events - Application Event Handler
 *******************************************************/

USB_DEVICE_CDC_EVENT_RESPONSE APP_USBDeviceCDCEventHandler
(
        USB_DEVICE_CDC_INDEX index,
        USB_DEVICE_CDC_EVENT event,
        void * pData,
        uintptr_t userData
        ) {
    APP_DATA * appDataObject;
    appDataObject = (APP_DATA *) userData;
    USB_CDC_CONTROL_LINE_STATE * controlLineStateData;

    switch (event) {
        case USB_DEVICE_CDC_EVENT_GET_LINE_CODING:

            /* This means the host wants to know the current line
             * coding. This is a control transfer request. Use the
             * USB_DEVICE_ControlSend() function to send the data to
             * host.  */

            USB_DEVICE_ControlSend(appDataObject->deviceHandle,
                    &appDataObject->getLineCodingData, sizeof (USB_CDC_LINE_CODING));

            break;

        case USB_DEVICE_CDC_EVENT_SET_LINE_CODING:

            /* This means the host wants to set the line coding.
             * This is a control transfer request. Use the
             * USB_DEVICE_ControlReceive() function to receive the
             * data from the host */

            USB_DEVICE_ControlReceive(appDataObject->deviceHandle,
                    &appDataObject->setLineCodingData, sizeof (USB_CDC_LINE_CODING));

            break;

        case USB_DEVICE_CDC_EVENT_SET_CONTROL_LINE_STATE:

            /* This means the host is setting the control line state.
             * Read the control line state. We will accept this request
             * for now. */

            controlLineStateData = (USB_CDC_CONTROL_LINE_STATE *) pData;
            appDataObject->controlLineStateData.dtr = controlLineStateData->dtr;
            appDataObject->controlLineStateData.carrier = controlLineStateData->carrier;

            USB_DEVICE_ControlStatus(appDataObject->deviceHandle, USB_DEVICE_CONTROL_STATUS_OK);

            break;

        case USB_DEVICE_CDC_EVENT_SEND_BREAK:

            /* This means that the host is requesting that a break of the
             * specified duration be sent. Read the break duration */

            appDataObject->breakData = ((USB_DEVICE_CDC_EVENT_DATA_SEND_BREAK *) pData)->breakDuration;

            /* Complete the control transfer by sending a ZLP  */
            USB_DEVICE_ControlStatus(appDataObject->deviceHandle, USB_DEVICE_CONTROL_STATUS_OK);

            break;

        case USB_DEVICE_CDC_EVENT_READ_COMPLETE:

            /* This means that the host has sent some data*/
            appDataObject->isReadComplete = true;
            break;

        case USB_DEVICE_CDC_EVENT_CONTROL_TRANSFER_DATA_RECEIVED:

            /* The data stage of the last control transfer is
             * complete. For now we accept all the data */

            USB_DEVICE_ControlStatus(appDataObject->deviceHandle, USB_DEVICE_CONTROL_STATUS_OK);
            break;
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

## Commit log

2017-09-17 TL01 Files
    [Accouplement-B14.SLDPRT, Accouplement-MB10.SLDPRT, Accouplement-MB11.SLDASM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]
2017-10-26 Added some parts and reference material
    [lighthouse_mount.stl, lighthouse_spacer.stl, pcb_mount_1.stl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]
2017-10-27 Vive sensors implemented, basic line-following behavior
2017-11-08 Mapping of track data complete
2017-11-08 fixed x,y discrepency in vive calculation, recalibrated for new servo, changed backup behavior for line following
    [app.c, app.h]
2017-12-03 Proportional steering control implemented
2017-12-03 Added PCB shield files
    [shield_2016.brd, shield_2016.sch]

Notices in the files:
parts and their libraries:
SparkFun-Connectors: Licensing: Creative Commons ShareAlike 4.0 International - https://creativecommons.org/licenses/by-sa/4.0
